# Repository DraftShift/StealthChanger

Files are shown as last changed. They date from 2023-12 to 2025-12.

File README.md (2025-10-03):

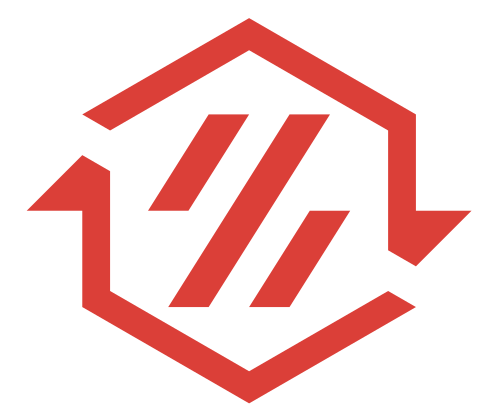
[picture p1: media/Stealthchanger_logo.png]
#  StealthChanger
**Tool changing system for Vorons and other front mount printer motion systems.**


&nbsp;&nbsp;&nbsp;&nbsp;&nbsp;&nbsp;


## Introduction

Unlike the name suggests we support more then just stealthburner.

Due to difficulties with heat insert and aligning of bearings and mounts we wanted to try a more simplistic design based on bushings and pins.

This is a very light design, requiring less parts and as such is cheaper and easier to build.  Input shaper tests have shown it to be as rigid if not more than current Tapchanger.

All parts are easily replaceable without reprinting if wear happens, life of the bushings and pins are still being tested.

## Tool compatability
Currently we support the standard Stealth Burner, Dragon Burner, Rapid Burner, Yavoth, AntHead, A4T, XOL, Jabberwocky and Archetype BlackBird.  There is also a usermod for the [Mini Stealth Burner](UserMods/jdmontgomer/MiniSB_SC).

## V1.1 Release
The original StealthChanger shuttle and backplates have been updated to V1.1, this update is to improve rigidity and probe accuracy. To help identify the version, "V1.1" has been clearly marked on all shuttles and backplates. please note, V1.1 is NOT compatible with previous versions. Updated documentation will follow shorly.
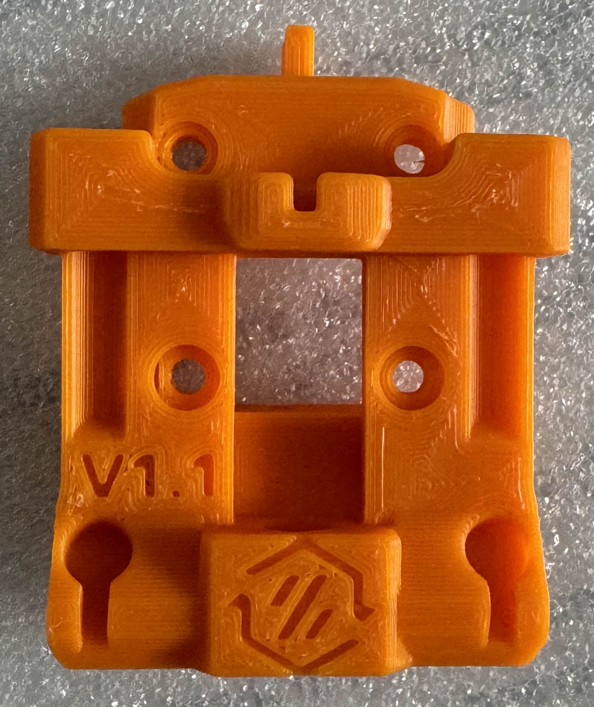
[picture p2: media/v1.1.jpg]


## Documentation and Info

Please use our [wiki](../../wiki) for more information and documentation.

- [Bill of Materials](../../wiki/Bill-of-Materials)
- [Docks](../../wiki/Docks)
- [Printing](../../wiki/Printing)
- [Assembling](../../wiki/Assembling)
- [Installation](../../wiki/Installation)
- [Configuration](../../wiki/Configuration)
- [Calibration](../../wiki/Calibration)
- [Slicers](../../wiki/Slicers)
- [Serials](../../wiki/Serials)
- [Support and FAQs](../../wiki/Support-and-FAQs)
- [Contributing & Donating](../../wiki/Contributing-and-Donating)
- [Team & Credits](../../wiki/Team-and-Credits)
- [Vendors & Kits](../../wiki/Vendors-and-Kits)

## Preview
### Explaination Video featuring GMBridge
MRRF Interview (https://www.youtube.com/watch?v=iQx_yx1GapI)
### Printed Parts (Dragonburner) by BT123
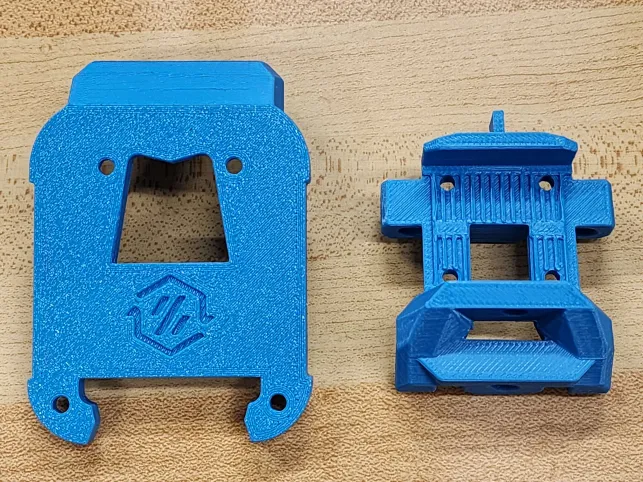
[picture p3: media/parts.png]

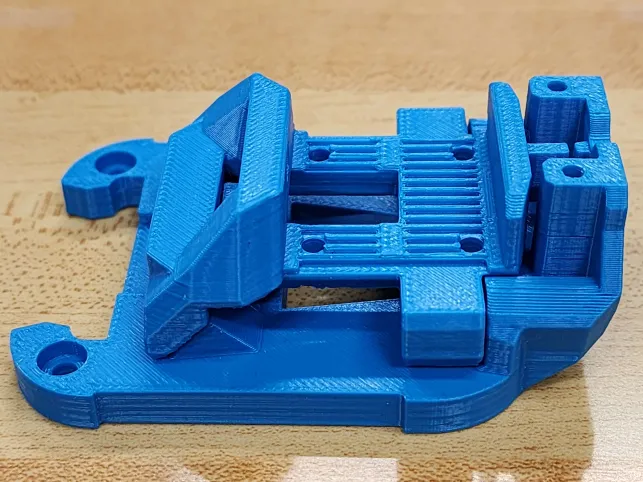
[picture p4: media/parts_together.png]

### Important! - Check for clear Hex's (Dragonburner) by BT123
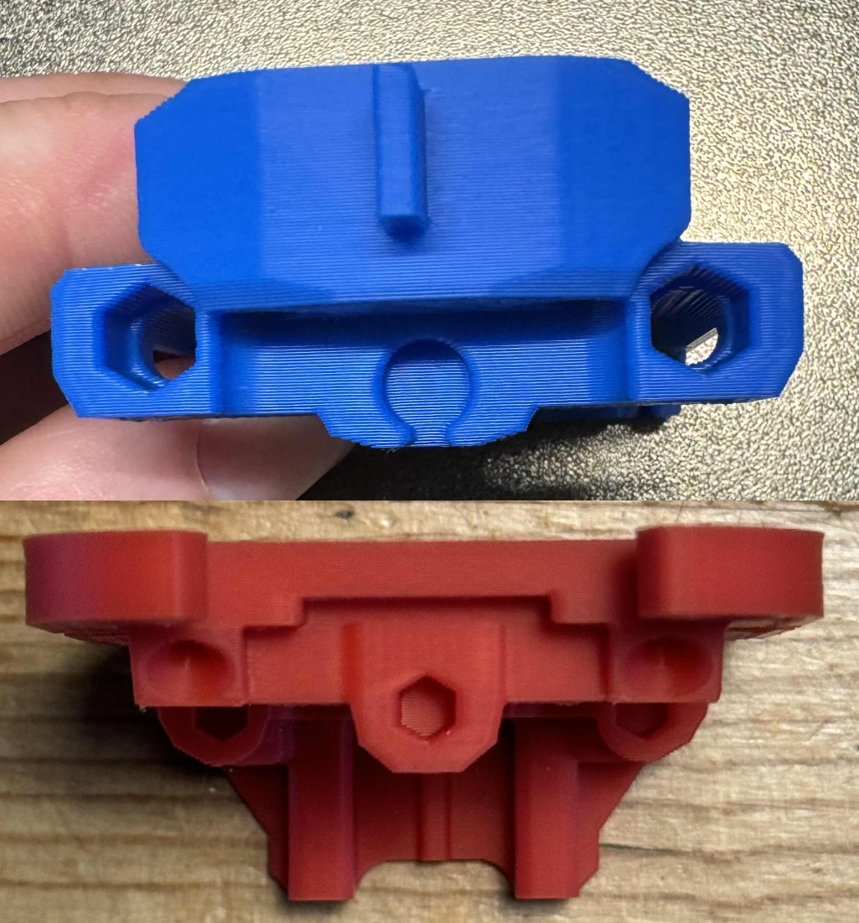
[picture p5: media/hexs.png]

### Assembled Shuttle and Backplate by BT123

### Motion (Stealthburner) by TheSin-

### Docking (Stealthburner) by fiferboy


Originally based on Viesturz's [Tapchanger](https://github.com/viesturz/tapchanger)

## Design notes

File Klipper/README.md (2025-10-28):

# Example Setup

Most of the code has been taken from the [TapChanger](https://github.com/viesturz/tapchanger) repo.

## Tapchanger Files

You need
- `homing.cfg`, `macros.cfg`, and `toolchanger.cfg` from [TapChanger Examples/per tool probe](https://github.com/viesturz/klipper-toolchanger/tree/main/examples/z%20probe/per%20tool%20probe)
- [`tool_detection.cfg`](https://github.com/viesturz/klipper-toolchanger/blob/main/examples/tool_detection.cfg)

You can either add them manually to your klipper install, or alternatively, you can integrate them to your config so that moonraker keeps them up to date with your other software if they change. Below are the steps for the integrated way. If you make any changes to the files though, they will be overwritten if you update. If you choose to manually add them, make sure your printer.cfg reflects the location of them.

**On the Klipper System** 
```
cd ~
git clone https://github.com/viesturz/tapchanger.git
ln -s ~/tapchanger/Klipper/config-example ~/printer_data/config/tapchanger
```

**Add to moonraker.conf**
```
[update_manager tapchanger]
type: git_repo
path: ~/tapchanger
origin: https://github.com/viesturz/tapchanger.git
primary_branch: main
managed_services: klipper
```

## Klipper Toolchanger

You must install [klipper-toolchanger](https://github.com/viesturz/klipper-toolchanger/), Follow instruction on the linked page.

## Toolheads

Toolchangers start with number 0, and count up. So for all the configs, make sure you change all sections. IE, in your T1 config, make sure its extruder1, fan1, etc. See the examples.  **NOTE: The only except to this rule is T0 extruder has no number.**

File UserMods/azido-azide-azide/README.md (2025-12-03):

# Monolith gantry with fixed beltpath issues which arises by using the monolith beltpath with the (cnc) stealthchanger shuttle
The belts are aligned by offsetting the X-axis from its previous location ~2.26mm to the back. When the CNC shuttle is used just clamp the belts only in the front.



## The file V2 mod. Monolith Stealthchanger compl. is a derivative work from CloakedWaynes monolith gantry. This gantry is modified to use mgn12 on all three axis  



## The file Sheetmetal 9mm AWD X-axis Stealthchanger compl. modifies just the monolith XY joints to fix the belt issues



## The file Printed 6mm 2WD X-axis Stealthchanger compl. modifies just the monolith XY joints to fix the belt issues



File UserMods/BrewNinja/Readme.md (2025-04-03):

Anthead Mods

 - There is an improved printing version of N3MI's Voron Sherpa spaced Stealthchanger main body. No supports needed.
 - Second version of N3MI's main body with more space above the diffuser/PCB. Read that folder for more info.
 - Thin SC diffuser for resin printing.
 - HGX adapter plate. This fits any of the anthead sherpa spacing bodies. You really don't need this except if you want to run the wires up the back.

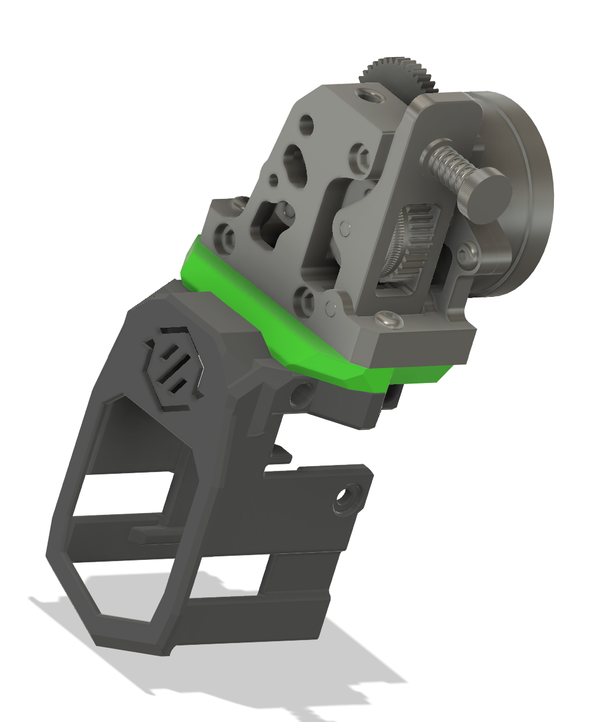
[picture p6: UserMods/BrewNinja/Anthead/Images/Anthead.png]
Anthead Mods Pic


If you have questions about any of my mods, you can find me on the Stealthchanger Discord.

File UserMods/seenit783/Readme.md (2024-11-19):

# EBB36 and Galileo 2 Standalone User Mod

## Overview

This user mod provides compatibility between the [EBB36](https://example.com/ebb36) and the [Galileo 2 Standalone](https://github.com/JaredC01/Galileo2/tree/main/galileo2_standalone) system. The mod enables seamless integration, allowing users to utilize these two components together efficiently.

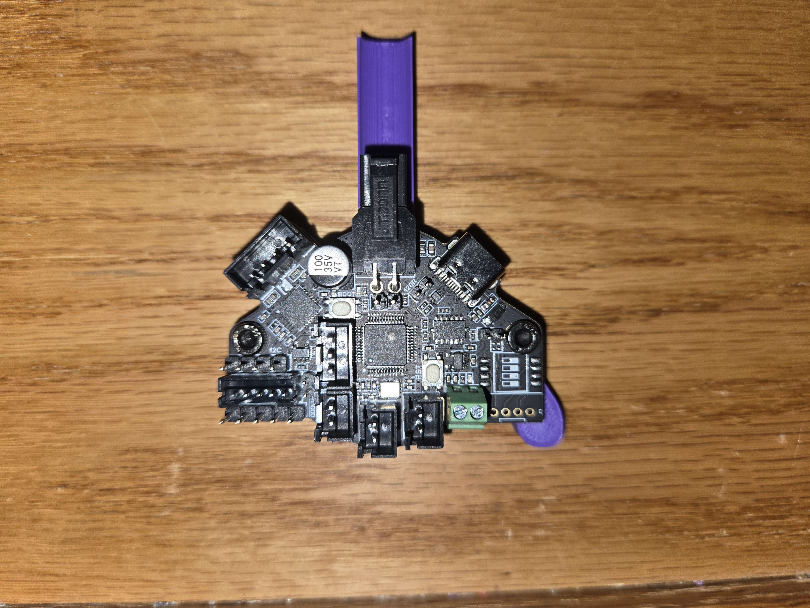
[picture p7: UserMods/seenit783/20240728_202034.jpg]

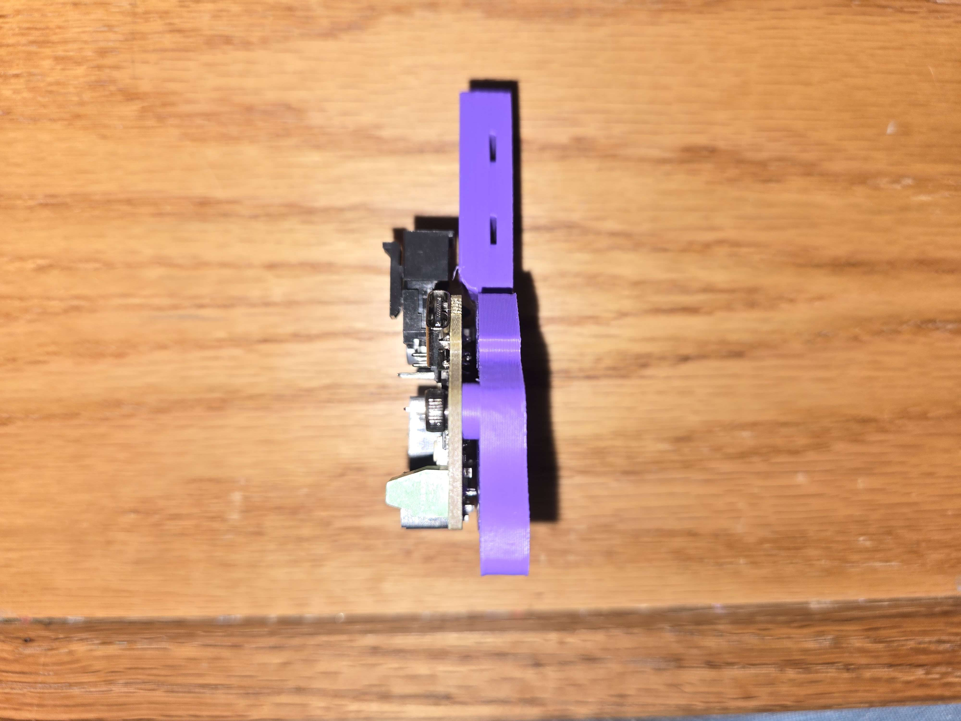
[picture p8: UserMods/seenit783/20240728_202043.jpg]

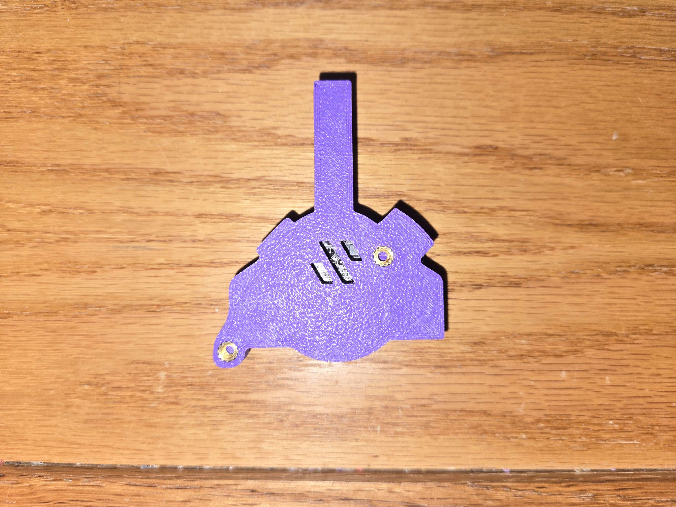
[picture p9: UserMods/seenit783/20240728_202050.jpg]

*Image of the Galileo 2 Stand Alone device*

Galileo 2 Standalone  
*Image of the Galileo 2 Standalone system*

## Features

- **Compatibility**: Ensures that the EBB36 can directly interface with the Galileo 2 Standalone.

## Installation
2 - M3x40 cap bolts with 100% Threads https://a.co/d/dL6dTwI 
4 - M3x5x4 Threaded inserts https://a.co/d/jbFK0In

1. **Download the Mod**: Obtain the latest version of the user mod from the [releases page](UserMods/seenit783).

2. Refer to the [Galileo 2 Standalone configuration guide](https://github.com/JaredC01/Galileo2/tree/main/galileo2_standalone) for detailed configuration instructions.

## Contributing

If you have suggestions for improvements or encounter bugs, please open an issue on the [GitHub repository](https://example.com/issues). Contributions are welcome, and you can submit a pull request to enhance the mod.

## License

This mod is licensed under the [MIT License](https://example.com/license). See the `LICENSE` file for more details.

## Contact
Angus MacLeod On Discord

For further assistance, you can contact the mod author at [richardferrington@gmail.com](mailto:richardferrington@gmail.com).
Angus MacLeod on Discord
---

Thank you for using the EBB36/Galileo 2 Standalone User Mod. We hope it enhances your experience with your toolheads!

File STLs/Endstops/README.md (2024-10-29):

# Endstops

There are a few options availble for x/y endstops. All options remove the X chain as it's not used with SC at all.

1. Hall Effect: Using the normal Voron X/Y Join hall effect board, download and print the [Hall_Effect.stl](Hall_Effect.stl) or [Hall_Effect_Shuttlekepper.stl](Hall_Effect_Shuttlekepper.stl) if you are use shuttle keeper.

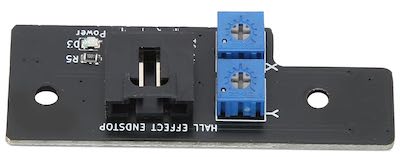
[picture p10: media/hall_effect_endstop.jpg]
Hall Effect board


2. Switches: Using the normal Voron X/Y Join switch board (both switches are on the x/y join together like hall effect.  Download and print the [Hall_Effect.stl](Hall_Effect.stl) or [Hall_Effect_Shuttlekepper.stl](Hall_Effect_Shuttlekepper.stl) if you are use shuttle keeper, this will add the needed surface for the X switch to hit.

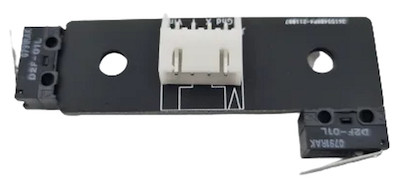
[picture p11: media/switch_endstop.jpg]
Switches board


3. Relocated Switches: This will relocate both X/Y to the rear A Motor brackets.  This has the added benefit of removing the Y chain completely.  Download and print [[a]_switch_bracket.stl]([a]_switch_bracket.stl) and [[a]_switch_arm.stl]([a]_switch_arm.stl).

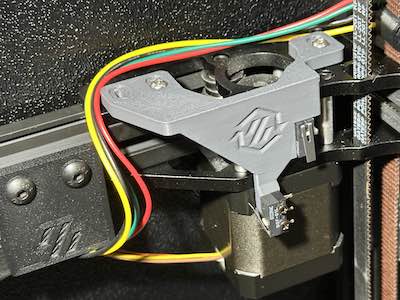
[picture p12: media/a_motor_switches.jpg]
Relocated Switches


4. Sensorless: Of course you always have the option of sensorless homing for X/Y which also allows you to completely remove the Y chain.  But you have less wires and nothing to print in this case.

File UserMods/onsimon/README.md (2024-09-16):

# Orbiter V2 BTT EBB36 carrier

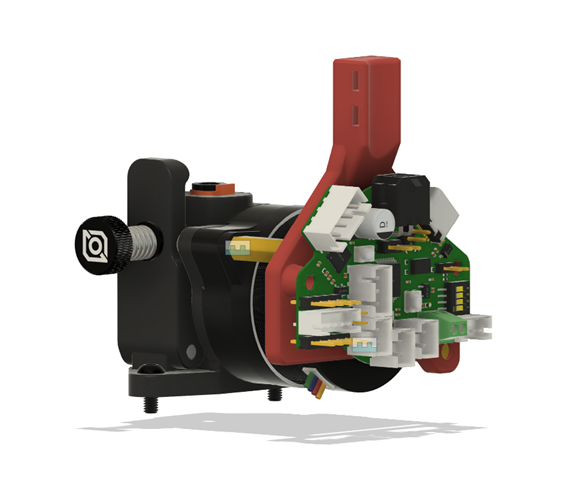
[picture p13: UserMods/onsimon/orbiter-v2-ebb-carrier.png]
orbiter-v2-ebb-carrier
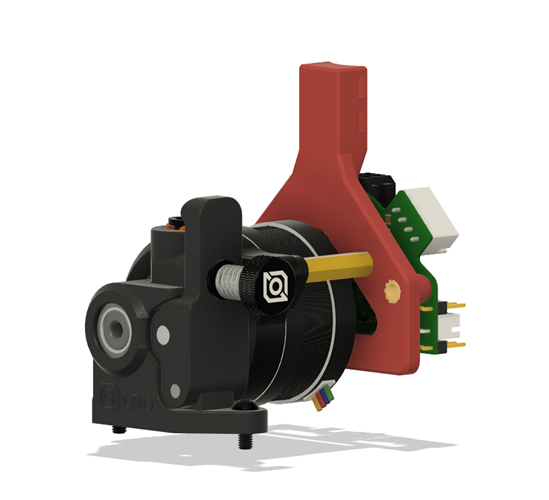
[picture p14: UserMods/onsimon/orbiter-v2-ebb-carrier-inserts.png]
orbiter-v2-ebb-carrier
 

Since the extuder motor on Orbiter V2 sits quite low, the EBB36 will interfere with the optotap PCB on some toolhead backplates (Dragon Burner and Yavoth, maybe more). So I created this PCB carrier that places the EBB36 a few mm higher than other existing mounts, and also tried to make it as rigid as possible without extra structures or modifications. 

Parts:
* Standoffs included with the EBB36
* 2 M3 BHCS to secure the mount agianst the standoffs
* 2 M3 SHCS to secure the EBB36 to the mount
* Optional: 2 M3 5x4 heat inserts (print the corresponding STL)

It is modelled to real-world dimesions and works fine as-is with ABS for me, but you can consider slicing with appropriate shrinkage compensation for your specific filament for the best possible fit.

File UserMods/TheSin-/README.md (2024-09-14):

# Mods to Stealthchanger v1.x

- **Hall Effect Bracket** with a 5mm shift to deal with shuttle keeper moving the shuttle out 5mm. Hall Effect setup comes from the Voron Team in the original 2.4R2 CAD

- **Z stop** is an original design and allows for the shuttle to use a standard Voron Z End Stop to home the shuttle without a tool or to avoid using tap to home.

- **SV08 Dockbar Brackets**

- **PCB36 Mount** is an Fly SHT36/Nitehawk 36 PCB mount for SC with HGX CNC/Orbitor2 Extruder.  Requiers a 20mm standoff.  Original PCB mount is from [MapleLeafMakers](https://github.com/MapleLeafMakers), updated to fit V3.

- **Belt Covers** For Voron v2, orignal from [Akio in the Voron Usermods](https://mods.vorondesign.com/details/LzEFU0RDHXUarF7y69x2Q), build with the SC Logo in open or raised for 2 colour printing

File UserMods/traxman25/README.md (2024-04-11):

## 5.5mm OD Bushing mod
Mod to the stock Stealth Changer shuttle to use 5.5mm OD bushings from Mc MasterCarr. More info and a link to the bushings is included in that directory. 

## Custom Dragonburner upgrades
These parts mod the Dragonburner tool head with optional numbered cowl and EBB36 mount. The EBB36 mount is designed to work with the Orbiter v2.0 extruder on the tall mount.

Original cowl by chirpy2605 [here](https://github.com/chirpy2605/voron)

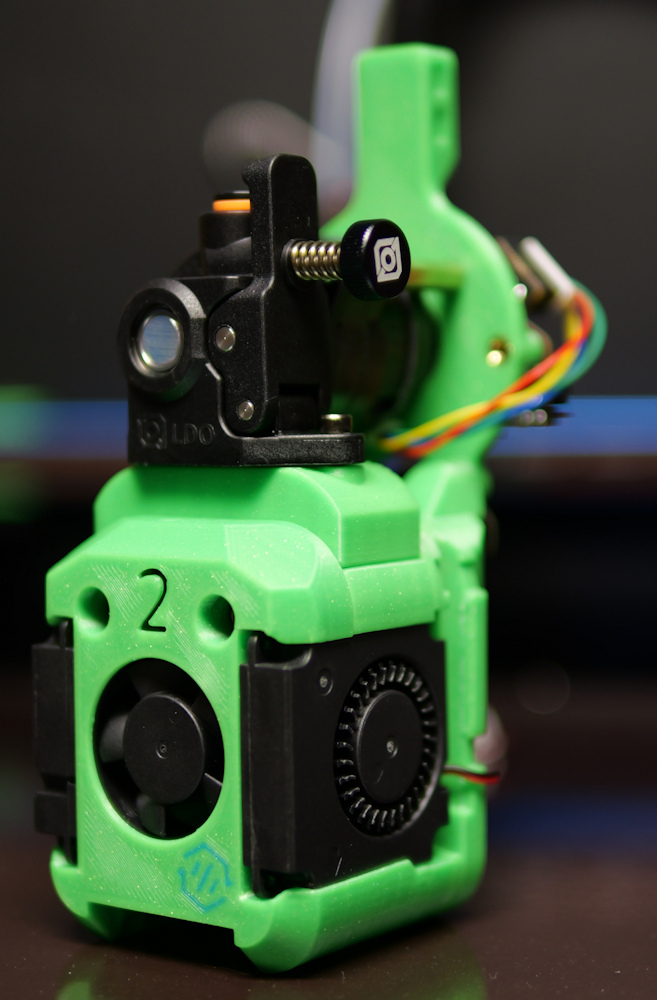
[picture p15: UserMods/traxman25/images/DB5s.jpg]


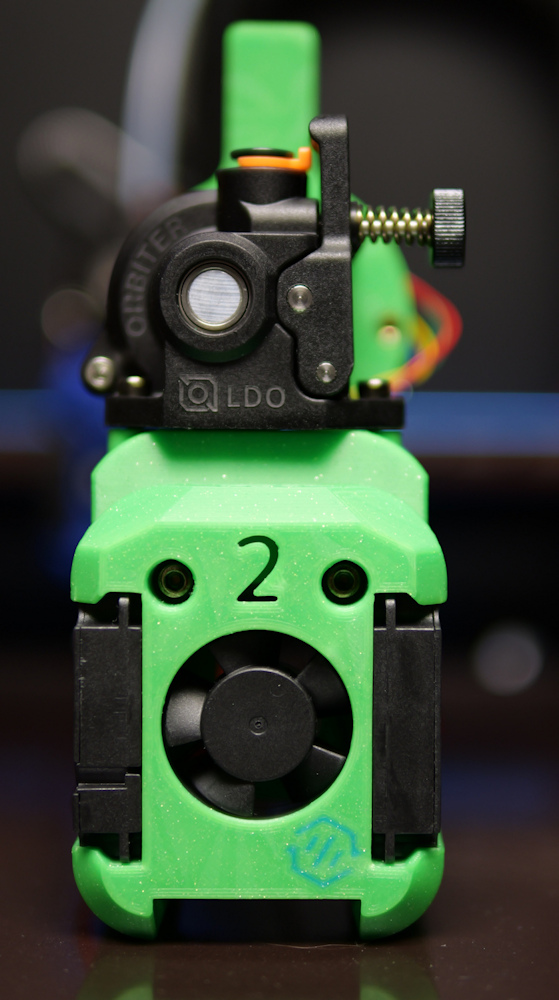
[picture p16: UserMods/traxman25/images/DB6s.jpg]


## Custom Dragonburner Cowls
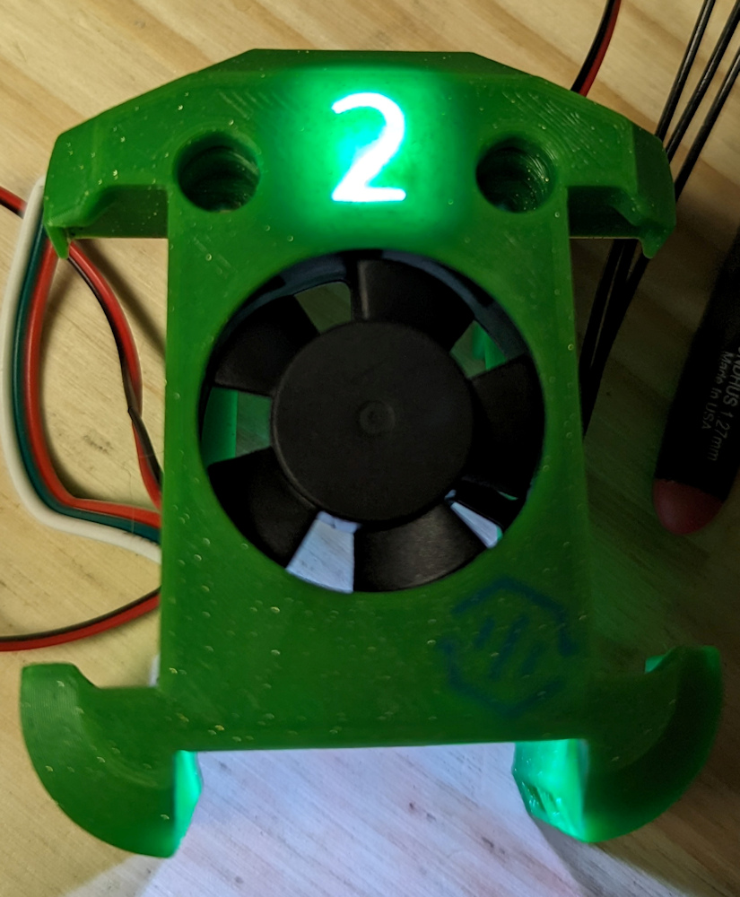
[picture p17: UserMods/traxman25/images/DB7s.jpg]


A series of Tap Changer Hook On Dock style Cowls based on Viesturz modification of Chirpy2605’s Dragonburner Cowl [here](https://github.com/viesturz/tapchanger/blob/main/Tapchanger/STL/Toolheads/DragonBurner/Cowling.stl).  These are modified to have the upper tool head light display the tool number. The Stealth Changer logo is applied as a second object (color) in the lower right corner. The STEP file for each tool head has the SC Logo embedded. To make them multi colored simply open each numbered cowl in your slicer as one object and then change the color for each part.

Also included are the numbered diffusers for each number. Numbers available are 0-6 so you can do up to 7 tools or pick and choose if you want them to start with 0 or 1.

You’ll also need the LED carrier for whichever LED you’ll be using. The RGBW Carrier is for the round 3 wire LEDs that are similar to what is included in the LDO kits. A carrier for Sequin LEDs is also provided for the small RGB Sequin LEDs that have 4 solder pads on them. Generally speaking, the round RGBW LEDs are much easier to wire.

A build plate with all tool heads and parts already oriented is provided. You’ll need to clone whichever version of the LED mount that you need and delete the one you don’t need. DB Numbered tool heads.3mf

## Dragonburner_EBB36_SC_Mount
All 3 parts described below are included in the DragonBurner_EBB36_OrbiterV2_mounts.STEP step file, and also on a pre-oriented and pre-support painted build plate in the .3mf file. 

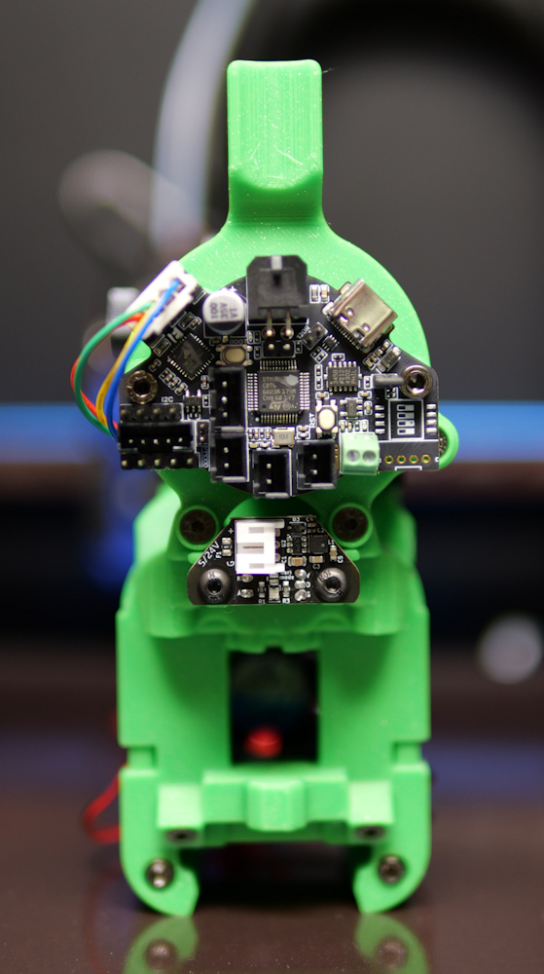
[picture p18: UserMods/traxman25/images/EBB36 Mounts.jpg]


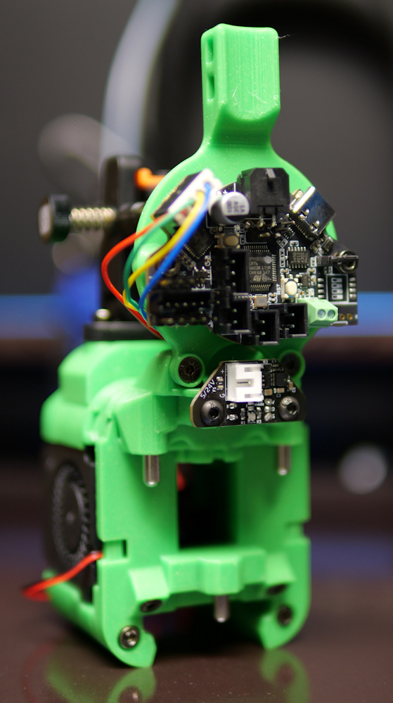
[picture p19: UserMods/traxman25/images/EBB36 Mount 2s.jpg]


### Dragon Burner EBB36 Backing Plate 
The only change to this part is adding the tool head PCB mount support ears to the top. These 2 holes will get an M3 heat set insert. This is modified from Stealthchanger’s back plate.

### EBB36 mount
Mounting plate with lower support screw holes that is similar to Chirpy2605’s mount. However, Chirpy2605’s original mount interferes with the DB Backing Plage. This mod also centers the EBB36 to the tool head assembly better.

Chirpy2605’s original version from [here](https://github.com/chirpy2605/voron/tree/main/general/PCB_Mounts/STLs)

### Orbiter V2.0 Extended Dragonburner Mount 
Minor cosmetic change to Chirpy2605’s Extended Dragonburner Orbiter V2.0 Mount. Unused holes that show above the cowl are removed.

The original mount is available [here](https://github.com/chirpy2605/voron/blob/main/general/Alternative_Voron_Mounts/Extended_Extruder_Mounts/Orbiter2_Extruder_Mount.stl)

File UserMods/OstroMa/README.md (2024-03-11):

# Mods for Stealthchanger

Dragonburner cowl mods based on work from the orignal cowl by [chirpy2605](https://github.com/chirpy2605/voron)

## Cowl moded to use the tapchanger hookon dock

## Numeric diffusers which are clip in to the Voron logo on Dragonburner and should work with Stealthburner

## 6 colour calibration print to help set x/y offsets between tools

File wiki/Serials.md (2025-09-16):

1. [Requests](#requests)
2. [List](#list)

## Requests

**Serial Application Guide Lines**

**Make sure media is 25MB or less (youtube link allowed, no limit)**

**Only one post per serial request**

**Post a video here that shows (we shouldn't need to pause, zoom, jog a video, it's your responsibility to make sure it's clear and easy to see at normal play speed)**

* 2 tool min print (mid print is fine)
* clearly shows a tool change
* clearly shows the StealthChanger shuttle
* a picture of the finished print is a bonus!
* some form of visual with your discord username and date (within the last 24 hours) on it in the video

**NOTE: tool calibration prints do not count**

Submit the request to the `#serial-request` channel on our [Discord](https://discord.gg/jJs73c6vSc).

## List

The list is available on our [Discord](https://discord.gg/jJs73c6vSc) in the `#serials` channel.

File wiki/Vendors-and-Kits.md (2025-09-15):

Currently we are working with Manufacturers and Vendors on official kits and CNC parts.  Once available and officially tested they will be listed here in alphabetical order.

# World Wide Vendors World Wide

## [LDO Motion](https://ldomotion.com/)

Each kit bellow includes a `Where to buy` on the product page.

- [Base Kit](https://ldomotion.com/products/16607023627247272)
  - CNC Shuttle
  - Sex Ball probe
  - NH-Hexa 6+1 port USB adapter
- [Tool & Dock Kit](https://ldomotion.com/products/16607023627247272)
  - Nitehawk-36 Toolhead Kit (SC-edition)
  - OptoTap PCB
  - RGB Sequin/NeoPixel
  - High CFM LDO fans (1x2510 axial, 2x4010 blower)
  - Backplate Pins
- [Top Hat & Door Buffer Kit](https://ldomotion.com/products/16607023627247272)
  - LDO quality extrusions
  - Fasteners and hardware
  - Panels

# Canadian Vendors Canada Flag

## [bobcat3d](https://bobcat3d.etsy.com/)
On Discord: Broncosis

- [Essential Hardward](https://www.etsy.com/ca/listing/1736497017/voron-stealth-changer-essential-hardware)
- [Opto Tap Sensors](https://www.etsy.com/ca/listing/1769077964/voron-opto-tap-sensors)

# USA Vendors US Flag

## [Fabreeko](https://www.fabreeko.com/)

- [Fysetc CNC Shuttle](https://www.fabreeko.com/products/stealth-changer-cnc-shuttle-kit-by-fysetc)
- [Fysetc Can Bus Distribution Board](https://www.fabreeko.com/products/can-bus-distribution-board-for-stealth-changer-by-fysetc)

## [Isik's Tech](https://store.isiks.tech/)
On Discord: xbst_

- [Birds' Nest](https://store.isiks.tech/products/birds-nest)
- [MOAR_CAN](https://store.isiks.tech/products/moar_can)
- [XT30+2 CAN Cable](https://store.isiks.tech/products/xt302-2-can-cable-3-meters)

# International Vendors

## [Fystec](https://www.aliexpress.com/store/3480083)

- [CNC Shuttle](https://s.click.aliexpress.com/e/_ooNmh4z)
- [Can Bus Distribution Board](https://s.click.aliexpress.com/e/_ooNmh4z)

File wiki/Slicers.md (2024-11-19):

1. [Slicer Software](#slicer-software)
2. [Slicer GCODEs](#slicer-gcodes)

## Slicer Software

| Name | Multitool | Issue | Discussion | Notes |
|:---:|:---:|:---:|:---:|---|
| Cura | <span style="color: green;">✓</span> | | | As of 5.8, select new printer, select DraftShift Design, select the size from the voron list, allows up to 8 extruders |
| OrcaSlicer | <span style="color: green;">✓</span> | | | As of 2.2 |
| PrusaSlicer | <span style="color: green;">✓</span> | | | |
| Simplify3D | <span style="color: silver;">?</span> | | | |
| Slic3r | <span style="color: silver;">?</span> | | | |
| SuperSlicer | <span style="color: green;">✓</span> | | | See [2197](https://github.com/supermerill/SuperSlicer/issues/2197) |

## Slicer GCODEs

### Prusa

Printer -> Custom G-code -> **Start G-code** - all must be a single line
```
PRINT_START TOOL_TEMP={first_layer_temperature[initial_tool]} {if is_extruder_used[0]}T0_TEMP={first_layer_temperature[0]}{endif} {if is_extruder_used[1]}T1_TEMP={first_layer_temperature[1]}{endif} {if is_extruder_used[2]}T2_TEMP={first_layer_temperature[2]}{endif} {if is_extruder_used[3]}T3_TEMP={first_layer_temperature[3]}{endif} {if is_extruder_used[4]}T4_TEMP={first_layer_temperature[4]}{endif} {if is_extruder_used[5]}T5_TEMP={first_layer_temperature[5]}{endif}  BED_TEMP=[first_layer_bed_temperature] TOOL=[initial_tool]
```

Printer -> Custom G-code -> **Tool change G-code**
```
M104 S{temperature[next_extruder]} T[next_extruder] ; set new tool temperature so it can start heating while changing
```

**NOTE**: add this as a second line if you use prime tower
```
G1 X{wipe_tower_x} Y{wipe_tower_y} F{travel_speed*60} ; Move to wipe tower before tool change
```

### Orca

Printer settings -> Machine G-code -> **Machine start G-code** - all must be a single line
```
PRINT_START TOOL_TEMP={first_layer_temperature[initial_tool]} {if is_extruder_used[0]}T0_TEMP={first_layer_temperature[0]}{endif} {if is_extruder_used[1]}T1_TEMP={first_layer_temperature[1]}{endif} {if is_extruder_used[2]}T2_TEMP={first_layer_temperature[2]}{endif} {if is_extruder_used[3]}T3_TEMP={first_layer_temperature[3]}{endif} {if is_extruder_used[4]}T4_TEMP={first_layer_temperature[4]}{endif} {if is_extruder_used[5]}T5_TEMP={first_layer_temperature[5]}{endif}  BED_TEMP=[first_layer_bed_temperature] TOOL=[initial_tool]
```

Printer settings -> Machine G-code -> **Change Filament G-code**
```
;Leave blank
```

### Cura

Machine Settings -> Printer -> **Start G-code** - all must be a single line
```
PRINT_START TOOL_TEMP={material_print_temperature_layer_0} T{initial_extruder_nr}_TEMP={material_print_temperature_layer_0} BED_TEMP={material_bed_temperature_layer_0} TOOL={initial_extruder_nr}
```

Machine Settings -> Printer ->  Tool n -> **Extruder Start G-code**
```
;Leave blank
```

Machine Settings -> Printer ->  Tool n -> **Pre tool change G-code** - 5.10+
```
M104 S{material_print_temperature} T{extruder_nr}
```

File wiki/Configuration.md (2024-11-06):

Toolchangers start with number 0, and count up. So for all the configs, make sure you change all sections. IE, in your T1 config, make sure its extruder1, fan1, etc. See the examples.  **NOTE: The only except to this rule is T0 extruder has no number.**

1. [Toolhead Configuration](#toolheads-configuration)
2. [CANbus](#canbus)
3. [Offsets](#offsets)
4. [Dock Positions](#dock-positions)
5. [close_y and safe_y](#close_y-and-safe_y)
6. [Docking Path](#Docking-Path)

## Toolheads Configuration

Please see the repo files for more info on these. [Configuration Files Repo](https://github.com/DraftShift/StealthChanger/blob/main/Klipper)

You need to add the info in `printer.cfg` from our repo to your `printer.cfg`

You need to have a separate toolhead config for each toolhead, then link those in your `printer.cfg`, as well as removing/moving the current extruder/hotend config from your `printer.cfg` file. See the examples in the repo for more information and a starting place. You will have to edit them with your own values.

**NOTE:** for some odd reason `t_command_restore_axis` was set to blank recently, this should be `t_command_restore_axis: z` please make sure that is your setting.

**NOTE:** `_PARK_ON_COOLING_PAD` is a useless macro in `PRINT_START` in `macros.cfg` please make sure to comment out or remove that line, currently it is line 129.

## CANbus

[Esoterical CANbus](https://github.com/Esoterical/voron_canbus) this is a pretty definitive guide for canbus implementation on klipper.

**Example CANbus layout**

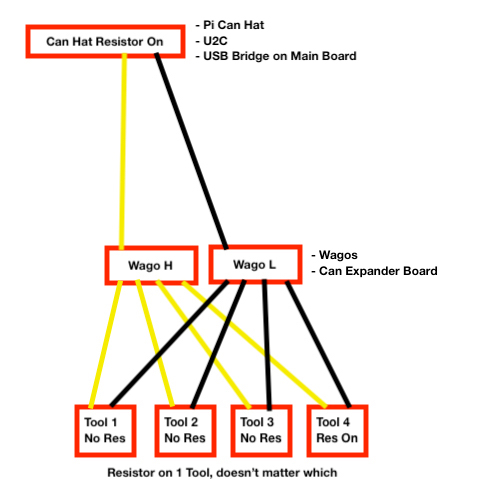
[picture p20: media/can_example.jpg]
Example CANbus Layout


## Offsets

There are 2 places to set offsets in your toolhead config files. There is gcode_(x/y/z)_offset in the [tool] section, and (x/y/z)_offset in the [tool_probe] section. These do different things. The ones in the [tool] section are always relative to a specific tool. IE, if you homed with T0, then the gcode offsets are relative to T0. When you do multi-material prints, you will have to choose 1 tool to always do the homing, even if you don't use it, because all the other offsets need to be set against it. The [tool_probe] offset is only ever applied when homing with that tool. The gcode offsets are applied when changing a tool.

You should set all the `[tool_probe]` offsets as well though. If you are only using a single tool, you can home with that tool, and it will use the offset in the `[tool_probe]` section. You won't need to home with your primary tool first then before you start a print. 

To try and further clarify. Lets say you have 3 tools, T0, T1, and T2. We will say that T0 is your "primary" tool. Setup the probe z_offset like you would any other printer. Make sure the offset is set in `z_offset` (IE, make sure when you home and go to Z 0, the nozzle is actually in that spot). Its location in x/y/z is always going to be 0 in relation to the other tools. So after T0 is homed, T1 and T2 (may) need to have their `gcode_(x/y/z)_offset` changed so they match the location that the primary tool actually is. There are 2 main ways of doing this. You can use a test print to print layers on top of or next to each other (something like this: [Nozzle Alignment Assist](https://www.printables.com/model/109267-nozzle-alignment-assist)) or you can use a camera (something like [kTAMV Klipper Tool Alignment](https://github.com/TypQxQ/kTAMV) or [IDEX Nozzle Calibration Tool](https://github.com/Life0fBrian/Brians-IDEX-Nozzle-Calibration-tool)).

## Dock Positions

When setting your dock position in your tool config, X and Y are pretty self explanatory. Put the tool in the right spot for it to sit. However, Z should be the point where 1 more mm down will untrigger the tap module. 

## close_y and safe_y

It is important to get this right. If you don't, you will have changing issues, or crash your tools into your docks. This is where we recommend you start:

- close_y = park_y + 30
- safe_y = park_y + thickness of your thickest tool (plus a little buffer)

IE, if you Y park position is -15. Your close Y should be 15. If your Y park position is 0, it should be 30. Safe Y should be slighty further out. 

## Docking Path

The docking path can be confusing for people to understand. Let's try to disect it. Take this path:

params_sc_path: [{'y':9.5 ,'z':4}, {'y':9.5, 'z':2}, {'y':5.5, 'z':0}, {'z':0, 'y':0, 'f':0.5}, {'z':-10, 'y':0}, {'z':-10, 'y':16}]

When looking at this, understand that the movements are relative to the park position. When dropping off a tool, it will go left to right, and when picking up a tool, it will go right to left on movements. Let's say your park position is x=20 y=-10, z=240 and close_y=20. When dropping off a tool, it will move up and start the sequence essentially at x=20 y=20 z=240. Now add in the first set of items. 

*  {'y':9.5 ,'z':4} Move to x=20 y=-0.5 z=244
*  {'y':9.5, 'z':2} Move to x=20 y=-0.5 z=242
*  {'y':5.5, 'z':0} Move to x=20 y=-4.5 z=240
*  {'z':0, 'y':0, 'f':0.5}. This will slowly move you (f is speed in gcode) to docking position of x=20 y=-10, z=240
*  {'z':-10, 'y':0} Drop the z down to z=230 so that it starts unhooking.
*  {'z':-10, 'y':16}. Move to z=230 y=6, we are clear of the tool.

It will then move to the close_y and x of the tool its picking up, and run in reverse order.

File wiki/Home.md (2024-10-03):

#  StealthChanger

Stealth Changer is a friction and magnetic fit, 3d printing multiple tool changer for the Voron 2.4 printer.

The purpose of a multiple toolhead changer is to allow for mixed material and mixed color printing without having to manually swap filament or purge filament during the swapping of materials. This allows for faster printing and less wasted filament compared to manual swapping and multi-material units like the ERCF or an AMS system.

It consists of a toolhead shuttle, toolhead backplate, and a optotap sensor for Z probing.

Stealth Changer supports a number of popular toolheads by mounting a backplate to the toolhead while using existing toolhead mounting points.

The shuttle replaces the current Voron TAP or Voron X carriage frame while using the TAP optotap sensor.

Mounting of the toolhead with the shuttle is done by using bushings and pins, with magnets to help create a strong mounting connection for high-speed printing while also providing better inputshaping results than TAP.

This is a very light design, requiring less parts and as such is cheaper and easier to build.  Input shaper tests have shown it to be as rigid if not more than current Tapchanger.

All parts are easily replaceable without reprinting if wear happens, life of the bushings and pins are still being tested.

The number of docks that can be installed is based on the width of the printer and the X/Y joins that allow the shuttle to reach the left and right side docks.

## Tool compatability
Currently we support the standard Stealth Burner, Dragon Burner, Rapid Burner, Yavoth, XOL and Archetype. There is also a usermod for the [Mini Stealth Burner](../blob/main/UserMods/jdmontgomer/MiniSB_SC).

## Before you begin

Make sure to visit our [Checklist](Checklist)

There are a few considerations that should be taken into account before you begin this project. First is, yes, you need an optotop board on every tool. The board is needed as thats how klipper knows which board is active. When the tap sensor is triggered, it knows which tool it has. You do not need the other tap parts though, like the MGN9 rail. StealthChanger by design also acts like the normal tap and does z probing.

Are you going to be printing any material that needs an enclosed printer? If the answer is yes, then you will need a tophat on your printer (or longer vertical extrusions). Typically, it adds around 200mm to the top (give or take based on your specific build). 

Canbus is nearly a requirement. While technically you dont need to do canbus, getting that many wires to each tool and doing so in a way that they won't tangle is going to be a nightmare. That being said, cable management is a very big part of the process. Without it, the cables will get wrapped up around each other and cause issues. Having some kind of plan for umbilicals is a must when considering the project.

How are you doing docks? There are a few different ways of doing them, and what you choose is going to influence a lot of things. If you plan on using a stock Voron build, remember that you need to have clearance at the sides of the docks for the front idlers to go beside them. This will also influence number of tools. You also have the option of top rail mounted docks or crossbar docks. Crossbar docks are probably the most stable, as they ultimately can be more stiff. You can also do a crossbar plus topmount for even more rigidity. If you decide to go this route, then you really want to use 2040 extrusions for your front rails. This way you can still use all the stock voron doors/panels etc with the crossbar, as well as not have the idlers hitting the crossbar. Top mounted docks are completely acceptable though, they just have a little more movement to them. As an alternative option the team has created a printable [door buffer](https://github.com/DraftShift/DoorBuffer) that will give you a crossbar without requiremend to replace your current front frame.

1. [Bill of Materials](Bill-of-Materials)
2. [Docks](Docks)
3. [Printing](Printing)
4. [Assembling](Assembling)
5. [Installation](Installation)
6. [Configuration](Configuration)
7. [Calibration](Calibration)
8. [Slicers](Slicers)
9. [Serials](Serials)
10. [Support & FAQs](Support-and-FAQs)
11. [Contributing & Donating](Contributing-and-Donating)
12. [Team & Credits](Team-and-Credits)
13. [Vendors & Kits](Vendors-and-Kits)

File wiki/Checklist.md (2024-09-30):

 - [ ] Read and understand all the documentation
 - [ ]  Decide on the tools to use, See [Docks](Docks) for a calculation of how many will fit
 - [ ] Decide on dock types, [Modular Dock](https://github.com/DraftShift/ModularDock) or other
 - [ ] Decide if you are going top mount, or use a cross bar, 2040 or [Door Buffer](https://github.com/DraftShift/DoorBuffer) or [MiniBFI](https://github.com/DraftShift/StealthChanger/tree/main/UserMods/BT123/MiniBFI%20%2B%20MicroBFI)
 - [ ] Decide on a [Tophat](https://github.com/DraftShift/Tophat)
 - [ ] Decide on umbilical management **WIP**
 - [ ] Visit the [BOM](Bill-of-Materials) to make sure you have ordered everything you need for the convertion
 - [ ] Visit our [Printing](Printing) guide and start printing
 - [ ] At this point please inspect your prints, take extra note that your hexes are very uniform, if the tops are flat you will have alignment issues, it doesn't take much for things to start off wrong here.
 - [ ] [Assemble](Assembling) the shuttle and backplates
 - [ ] [Install](Installation) software
 - [ ] [Configure](Configuration) software
 - [ ] Calibrate [Z Offsets](Calibration#z-offset)
 - [ ] Calibrate [Dock Parking](Calibration#dock-parking)
 - [ ] Calibrate [X/Y Offsets](Calibration#xy-offset)
 - [ ] Registrer for a [serial](Serials)
 - [ ] Visit our [sponsor](https://github.com/sponsors/DraftShift) page

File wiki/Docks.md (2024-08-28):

The team has created their own dock as a solution. It allows for mounting from both the top bar, as well as a crossbar (or both). While its currently still in testing, its an option if you can do some work without having a full readme. You can view it here: [DraftShift Modular Dock](https://github.com/DraftShift/ModularDock)

Currently all docks used with [Viesturz's Tapchanger](https://github.com/viesturz/tapchanger) are compatible.

To calculate how many tools you can fit on the front of your printer you ened to know the tools to use first and the amount of room for your front idlers (stock gantry also can't move the entire length of X so make sure you factor that in as well.

   - Dragon Burners/Yavoth require 60mm per tool (I recommend 5mm between for extruder handles)
   - Blackbird, Stealth Burners and XOL require 76mm per tool
   - The gantry required about 20mm per side to be able to pass the tools.  To know how many tools you can fit it's simple math, measure that top bar -40mm to gantry and then divide the remainder by the size of your toolhead.

Once you have this add it all up and subtracked the length of your front extrusion.

Example: Voron 350 is 470mm total, 5 stealthburners is 76 x 5 = 380 -> 380 + 40 - 470 = 50, so that means you can fit 5 Stealthburners and have 50mm to spare which is not enoguh for any other tools.

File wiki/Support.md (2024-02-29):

1. [Methods](#methods)
2. [FAQs](#faqs)
3. [Build Guide](#build-guide)
4. [Macros](#macros)

## Methods

- For extra support join our [Discord](https://discord.gg/JhYY5BJe)
- For serial requests please see our [rules and how to](https://discord.gg/CjjZ4B5J)

## FAQs

1. After printing the parts make sure that the hex holes look to be proper hexes and that they are very uniform.  If they are misshapen chances are you need to reprint as you will have alignment issues.  It doesn't take much to be out by a lot.  Try printing at a slower speed if you have issues.

2. Calculating available size for tools (number of tools you can fit)
   - Dragon Burners require 60mm per tool (I recommend 5mm between for extruder handles)
   - Stealth Burners require 80mm per tool
   - The gantry required about 20mm per side to be able to pass the tools.  To know how many tools you can fit it's simple math, measure that top bar -40mm to gantry and then divide the remainder by the size of your toolhead.

3. Adjusting preload... Preload is created with the 2 countersunk screws in the tool plate.  These 2 screws need to be magnetic and will make contact with the magnets in the shuttle.  This adds 2 more wider points of contact at the base while also pre loading the sleeves/bearings.  To adjust them screw them all the way in, then slowly unscrew them 1/4 turn at a time (keeping each side even) until the tool no longer engages its self right away.  Once you reach a point where this happens, screw them back in 1/4 turn.  Each tool needs to be adjusted separately as printing irregularities can happen and this will allow you to compensate for it.  You may want to test and readjust these from time to time.

4. If you run homing on Z or QGL and you are getting lots of restarts or excessive runs.  Make sure you are using **N52** magnets, and check that your umbilicals are properly support and the right length.  If these 3 things aren't checked it will affect the tap precision.

5. A lot of people are asking which toolhead/extruder is recommended. The answer is whatever you want. The changer and tools are completely separate. That being said, using something that is already a tested combination for Stealth Burner or Dragon Burner is going to be the easiest.

6. CAN setup. You are definitely going to want to use CAN to connect your toolheads. Its only 4 wires and much lighter. You don't need anything fancy to split out the signal. Simple WAGO connectors work just fine. Of course, there are options for boards that will split the signal as well if you want something that looks a little more professional. Run wires up to the umbilical from your controller and power supply, then use WAGO's there to split the signal. See the guide here for a lot more CAN information: https://github.com/Esoterical/voron_canbus
   
7. If you try to change tools during a print (or when the hotends are active) and it drops off one tool, then waits behind another tool and does nothing, the issue is that its probably waiting for the tool temp to stabilize. Make sure you run a PID tune for each tool and place the info in the corresponding tool config.

## Build Guide
### Built on stream by [ZombieHedgehog](https://www.twitch.tv/zombiehedgehog)
| Episode | |
|--- |--- |
| 1 | https://youtu.be/YK2Zk2K584Y |
| 2 | https://youtu.be/yOGEAGLlvZc |
| 3 | https://youtu.be/W_r2b8U1J6k |
| 4 | https://youtu.be/cCbIjArKL4M |

## Macros

Tool_Align_Start - This macro will put the toolhead 100mm away from where you set the docking position. 
Tool_Align_Test - This macro will test the docking/undocking procedure. Start it from the docking position (start a few mm up on z, as the first movement is moving straight back on Y). 
Tool_Align_Done - This macro will move the toolhead back away from the dock.
A link to a video showing each one: [Youtube Video](https://www.youtube.com/watch?v=mOSi8zTpu_Q)

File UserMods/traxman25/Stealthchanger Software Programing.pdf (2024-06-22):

## Stealthchanger Software Programing

By: Traxman25
With parts and assistance from: Thessien
ComputerMedic
Klipper3d.org
Viesturz – Tap Changer project Frix-x – Shake Tune

You will need the following programs to complete this install: Raspberry Pi Imager (https://www.raspberrypi.com/software/) Notepad++ (https://notepad-plus-plus.org/downloads/)
WinSCP (https://winscp.net/eng/download.php)
Putty (https://www.chiark.greenend.org.uk/~sgtatham/putty/latest.html)

This guide is written for a Voron 2.4 350 Stealth Changer project with 6 tool heads. The hardware on this build is:
Raspberry Pi4B
Big Tree Tech Octopus v1.1 for the main drive motors
EBB36 tool head boards running either CanBus or USB communication For CanBus I used Big Tree Tech U2C
HDMI Screen
Big Tree Tech Filament Run Out Sensor V2.0
Orbiter V2.0 Extruders

The printer uses sensor less homing for X, and a Y switch moved into the A motor mount using this mod: https://github.com/VoronDesign/VoronUsers/tree/master/printer_mods/hartk1213/Voron2.4_Y_Endstop_Relocation (https://github.com/VoronDesign/VoronUsers/tree/master/printer_mods/hartk1213/Voron2.4_Y_Endstop_Relocation)

### Flashing Raspberry Pi firmware:

Raspberry Pi Imager (https://www.raspberrypi.com/software/)

Select your Raspberry Pi Device (Raspberry Pi 4)

Select the Operating System -> “Other Specific-purpose OS” -> 3D Printing -> Mainsail OS -> Mainsail OS

Choose Storage -> [choose the storage device you want to flash to]

Click Next - > Yes -> Yes. The installer will now write the Raspberry Pi firmware to the SD card.

Activating WiFi – On the flash drive will be a sample file called “wpa_supplicant.conf.example” Open this file in Notepad++ (You can not use Windows Notepad to generate this file) and follow the prompts for how to setup your specific wifi information.

Disconnect the flash drive

Insert the flash drive into the Raspberry Pi and power it on.

Note: If you have issues connecting the Pi via WiFi, connect via wired connection. Once the Klipper install is completed WiFi network details can be entered via the system settings in the Klipper Screen interface.

Once the Raspberry Pi is connected to your network log into it using Putty. (Host Name [name you gave the pi].local, or the IP address of the pi)

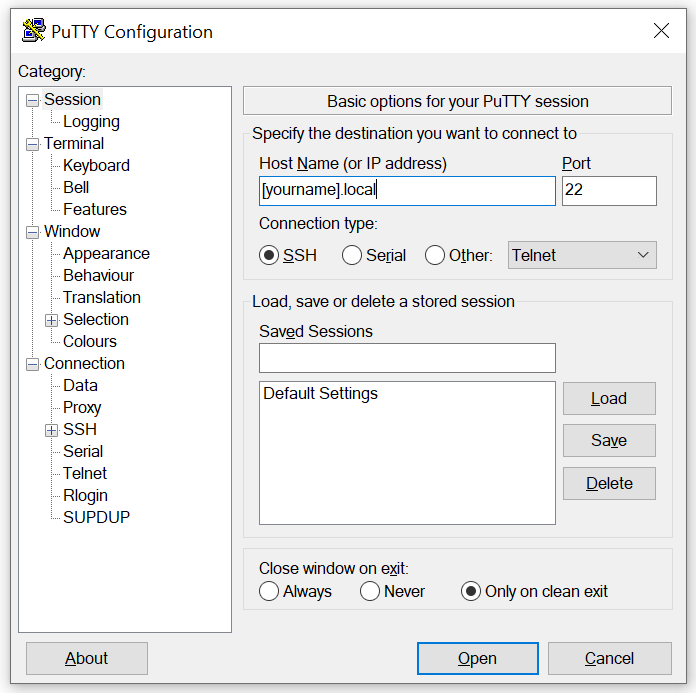
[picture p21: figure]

Enter the username and password you gave it while flashing the Pi OS.

Install git using the command:
sudo apt-get update && sudo apt-get install git

Install Kiauh using the command:
cd ~ && git clone https://github.com/dw-0/kiauh.git

Run Kiauh using the command:
./kiauh/kiauh.sh

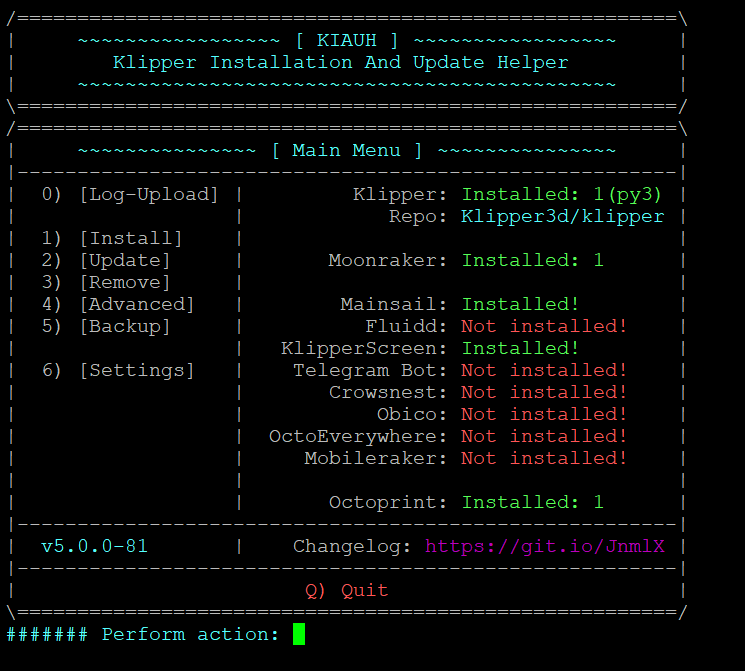
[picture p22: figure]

Press 1 enter to enter the Install menu

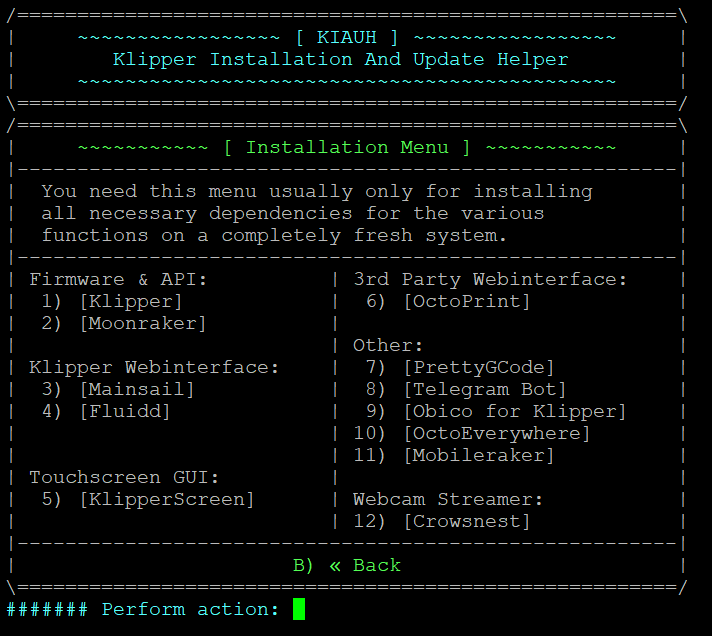
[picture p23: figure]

Install Klipper by entering 1 and following the prompts.

Complete the install by installing Moonraker, Mainsail or Fluid, KlipperScreen if you’re running a touch screen and any of the other optional applications that you’d like.

Once you’re done press B to go back.

### To flash the Firmware for the Octopus

Press 4 for Advanced

Press 2 for Build Only
Carefully setup the settings in the following menu according to the instructions for your control card:

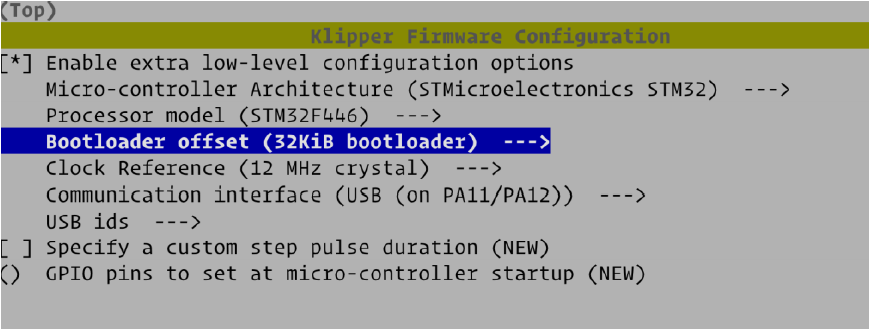
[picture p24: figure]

Press Q to Quit.

Press Y to write the Klipper.Bin file to the SD card.

Press B, then Q to quit.

Log into the pi with WinSCP.

Navigate to /home/(pi name)/klipper/out folder.

Either move the Klipper.Bin to the root folder of the flash drive, or download it to a folder you’ll remember.

Shut down the pi with the command sudo shutdown now

Remove the SD Card from the pi.

If you downloaded the Klipper.Bin file to your computer, connect the SD card to the computer and put the Klipper.Bin file onto the root directory of the SC card.

If you moved it using WinSCP you can put the flash drive directly into the control board.

Without the USB cable hooked to the pi, power up the control board. It will flash the firmware to the card in a few seconds.

Wait about a minute than power down the control card. To confirm the firmware was successfully flashed you can load the SD card and check that Klipper.Bin file name has been changed to Klipper.CUR

Reinsert the SD card into the Pi.

Hook up a USB cable from the USB A output on the Pi to the USB C input on the control card.

Boot up the pi and the control card.

ADXL RPi MCU install (Reference: https://www.klipper3d.org/RPi_microcontroller.html)

Install Raspberri Pi klipper MCU by entering the following command prompts
cd ~/klipper/
sudo cp ./scripts/klipper-mcu.service /etc/systemd/system/
sudo systemctl enable klipper-mcu.service

Make microcontroller code:
cd ~/klipper/
make menuconfig
Set “Microcontroller Architecture” to “Linux process” by pressing the down arrow to highlight Microcontroller Architecture, press the right arrow, down arrow down to Linnux process, press enter. Press Q
Press Y to save

Enter command prompt:

sudo service klipper stop
make flash
sudo service klipper start

Make sure the Linux SPI driver is enabled by running:
sudo raspi-config
and enabling SPI under the "Interfacing options" menu. (arrow down to option 3, right arrow to highlight <Select> hit Enter.

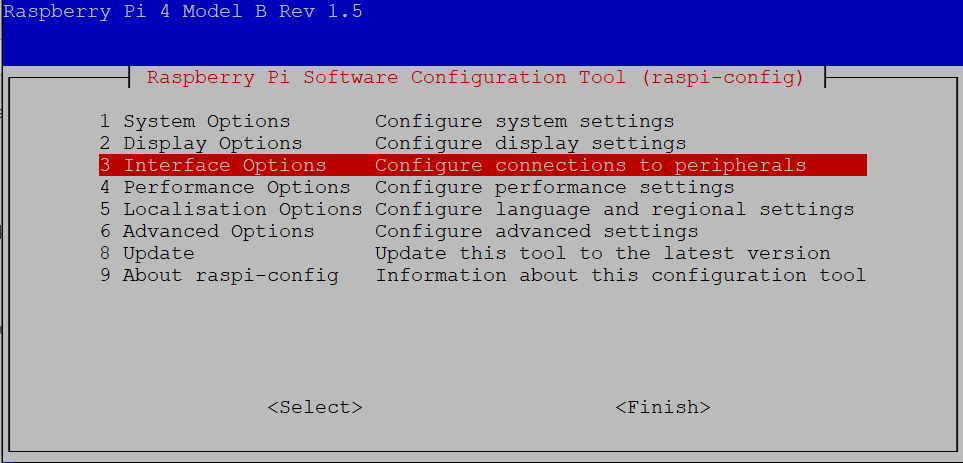
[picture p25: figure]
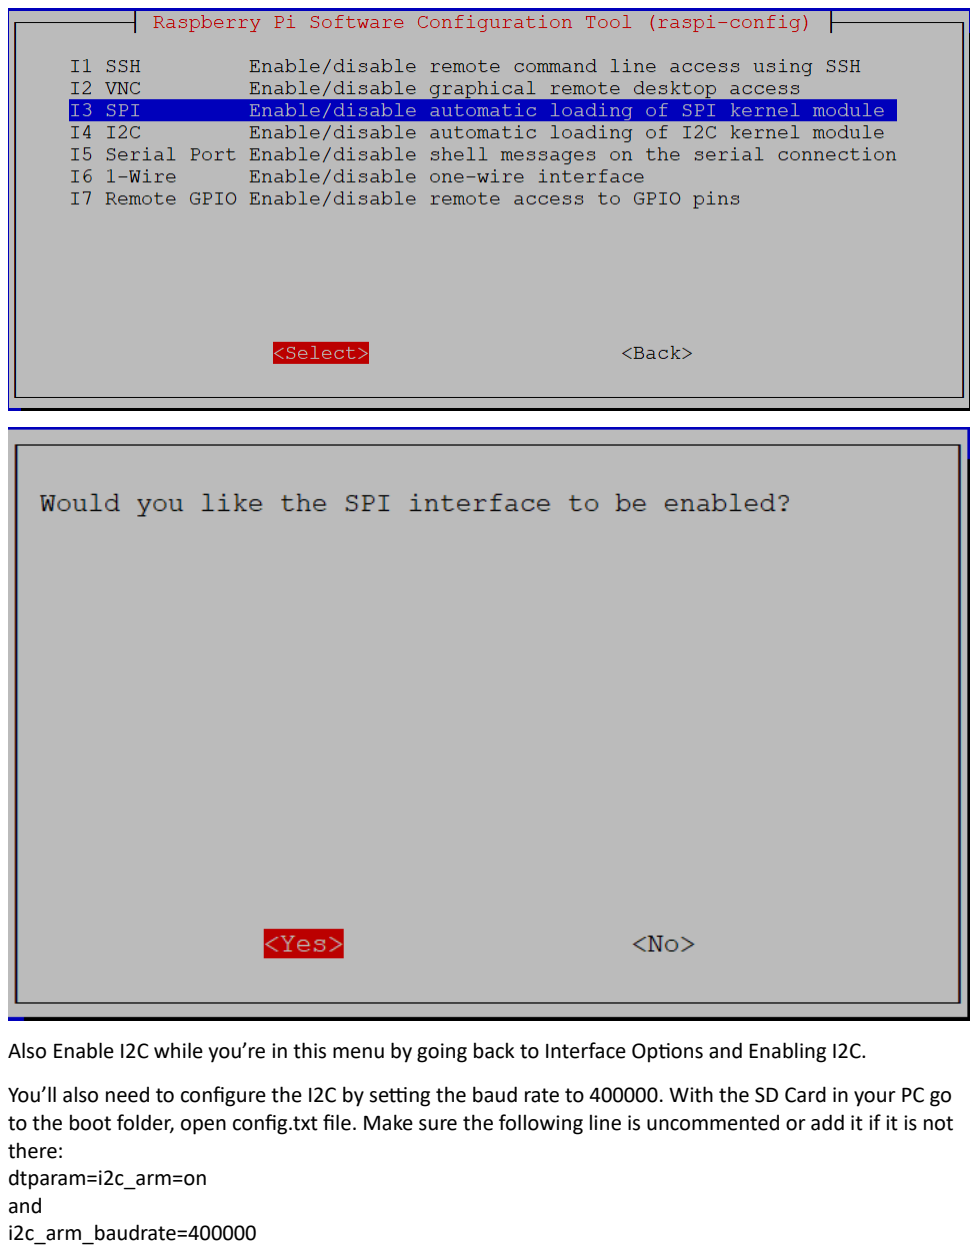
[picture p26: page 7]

Also Enable I2C while you’re in this menu by going back to Interface Options and Enabling I2C.

You’ll also need to configure the I2C by setting the baud rate to 400000. With the SD Card in your PC go to the boot folder, open config.txt file. Make sure the following line is uncommented or add it if it is not there:
dtparam=i2c_arm=on
and
i2c_arm_baudrate=400000

### Install Shaketune Input Shaper and Tuning Module (Reference: https://github.com/Frix-x/klippain-shaketune)

In putty enter command prompt:
wget -O - https://raw.githubusercontent.com/Frix-x/klippain-shaketune/main/install.sh | bash

(There is an additional step we will come back to later)

You should now have Klipper Screen working and be able to connect to the printer via a standard web interface. To log into the printer via a web browser you simple enter [printername].local or the IP address into your web browser address bar.

You will get an error message when connecting via the web browser, and on Klipper Screen. Ignore this for now.

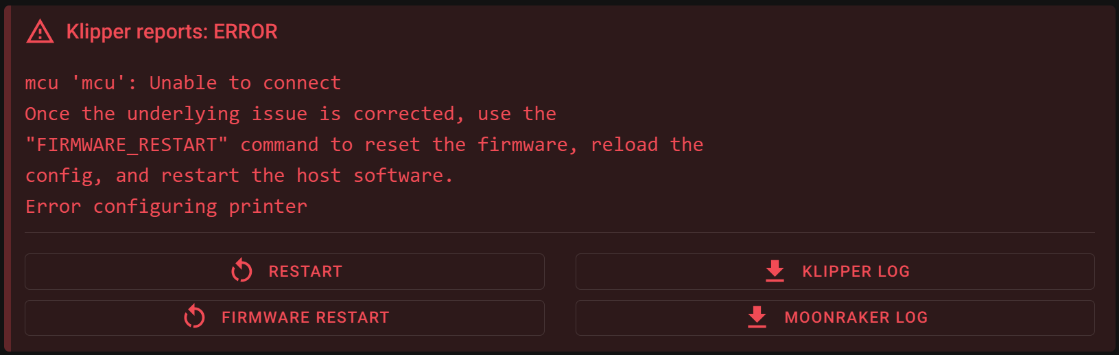
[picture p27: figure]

If you wish to connect via WiFi and had issues with that before, you can now go to Menu -> Network and select the network you wish to connect and enter the password.

On the Machine Tab, it is recommended to ensure all applications are up to date

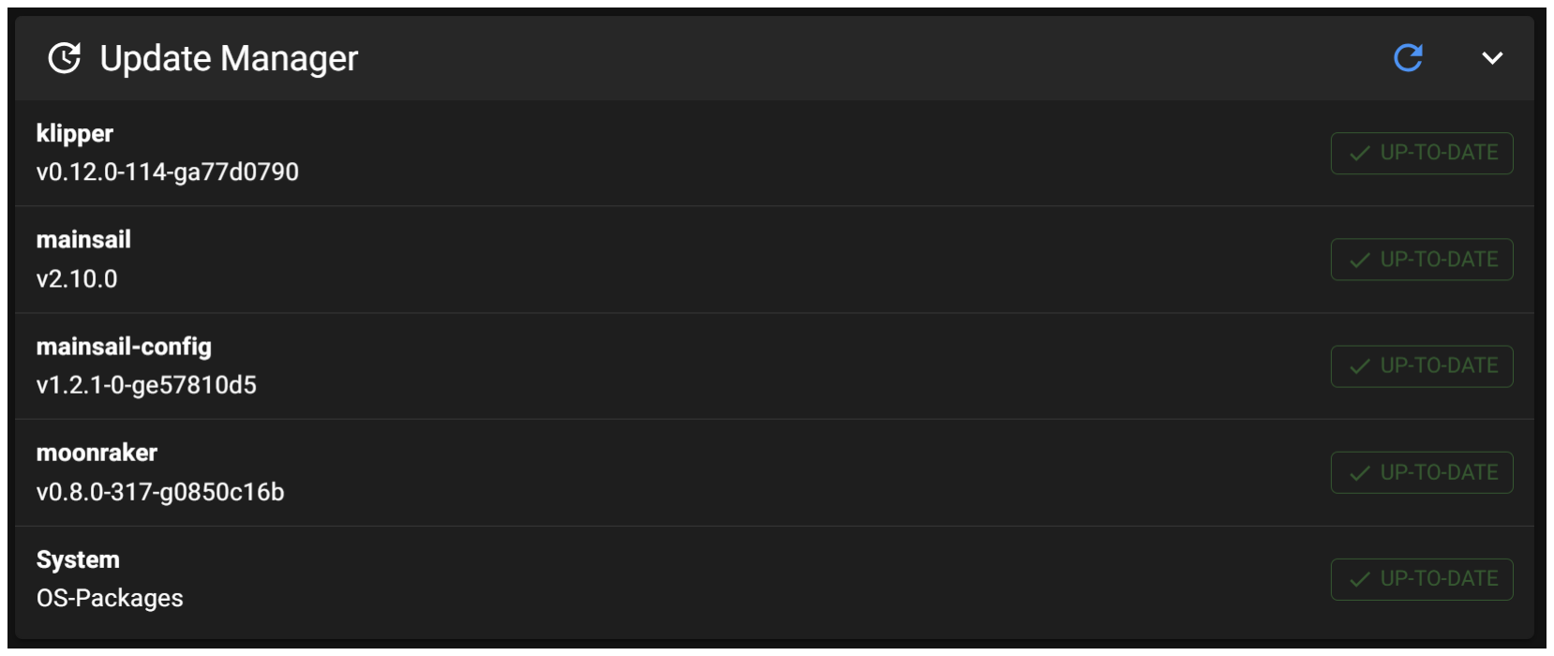
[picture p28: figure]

### ToolChanger Klipper Extension: https://github.com/viesturz/klipper-toolchanger

Run the following command in Putty:
wget -O - https://raw.githubusercontent.com/viesturz/klipper-toolchanger/main/install.sh | bash

Next to add toolchanger to the update section of Moonraker open moonraker.conf and add the following to the end of the file.
[update_manager klipper-toolchanger]
type: git_repo
channel: dev
path: ~/klipper-toolchanger
origin: https://github.com/viesturz/klipper-toolchanger.gitmanaged_services: klipper
primary_branch: main
install_script: install.sh
Also be sure to add the macros.cfg to your printer from the ToolChanger repo.

### Setting up printer.cfg

Starting with a stock Voron printer.cfg profile for your particular printer control board you’ll need to find the printer’s MCU ID. With the main printer control card plugged into the control computer, SSH into the controller and enter the command ls /dev/serial/by-id

This is your [mcu] serial address. Enter it after serial: /dev/serial/by-id/ as shown below.
Next is to include all of the sub configuration files. This allows settings and configurations to be located in separate files to help keep things manageable.

Below is a list of the files needed for a 6 tool changer. Homing.cfg is the custom homing override configuration. T0 through T5 is the configs for each individual tool head. Tool_detection.cfg is Also included is the config folder for ShakeTune.

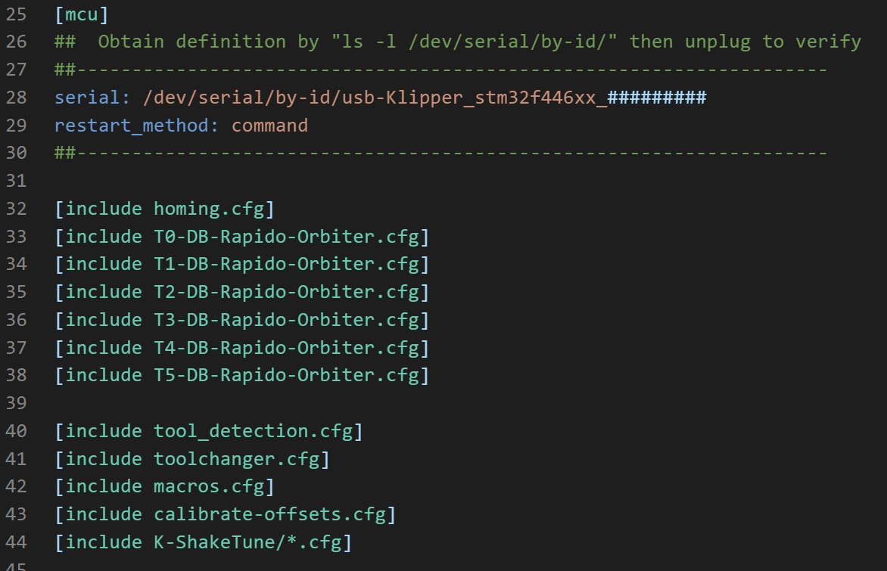
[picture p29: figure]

Add the [gcode_arcs], [rounded_path], and [excluding_object] sections as shown below.


If you’re using sensorless homing on x change the x endstop_pin to tmc2209_stepper_x:virtual_endstop

Also add driver_SGTHRS: 75 # 255 is most sensitive value, 0 is least sensitive below the stepper x section

Change Z endstop_pin to probe:z_virtual_endstop

Add the ADXL section shown below.


Add the [respond] and [force_move] sections as shown below

### Toolhead configs

Note: Tool head configs and pin addresses work a little differently with the tool changer. Tools are numbered starting a 0, so a 6 head tool changer would have tools 0 through 5.

Each tool head board is labeled by the mcu name that is given to it in the first line of the tool head board config file. Example shown below is tool 0 labeled et0 and tool 1 labeled et1. We’ll need this label as we build the pin callouts for each tool.

Each [function] section heading will need the tool head number after the label, except for on tool 0. Shown in the example below tool 0 extruder section is [extruder], tool 1 is [extruder1], etc.

Also each pin call out requires the tool head board name:pin# also shown in the example below. Example tool zero step_pin: et0:(pin#), tool 1 step_pin: et1:(pin#)

You’ll likely need to look up the pin numbers on the pin layout for the particular tool head board you’re using.

With the controller powered down hook up your tool head boards, boot up the controller, SSH into it and use ls /dev/serial/by-id to obtain all of the MCU IDs. Record the IDs that aren’t the main control board.

Download the toolhead sample config that matches your setup the closest from Viesturz tapchanger repo here: https://github.com/viesturz/tapchanger/tree/main/Klipper/config-example

If using Canbus for communication your MCU will be canbus_uuid: “ID number”
If using USB you will use the serial: “ID” style.

You’ll need to look up and enter your thermistor type.

It is easiest while setting up the printer to place the PID tune settings into the tool head config files rather than in the Save_Config in the main printer.cfg. This in case a tool head needs to be commented out then the Save_Config section does not need to be edited.


If you’re running headlight LEDs you’ll want to add the LED Control section into each tool head config Sequin LEDs usually use color_order: GRBW and have the initial_white: section

LED Sequins usually use color_order: GRB and do not use initial_white: section


The [tool T#] section contains the tool offset and park parameters for that tool.
Tool zero will have 0 for all gcode_offset values.

Params-type is the dock path type that is used during docking moves. We will address this a bit later

params_park_x y and z are where you will enter the physical location of that tool’s dock. As you’re setting up the config it is a good idea to enter an approximate location of the dock. Example your first dock will usually be X=25, Z close to the max z height of your printer. The next tools will be roughly +60mm in Y. We will fine tune these values later after initializing the printer and tuning z-offset.

Params_safe_y is the Y distance that is safe to for Z move up to the level of the docks.

Params_close_y is the Y distance that is save for x moves while moving from tool to tool, after dropping off a tool in it’s dock.

[tool_probe T#] is where you can adjust your probing samples, speed, retract distance, etc.
Pin is the pin number for the probe sensor
z-offset is that tools z-offset
speed is the downward z speed used during probing moves
Lift-speed is the upward z speed used to retract after the probe is triggered
samples is the number of probe samples taken at any given point
sample_retract_distance is the z height that the probe will raise between samples at a given point sample_tolerance is the allowable tolerance between probe measurements.
activate_code Heater=extruder(tool number unless zero) For tool zero leave the number off.

### toolchanger.cfg


Params_safe_y is the y distance that a loaded tool will safely clear the back of the parked tools. This will be used as the tools approach the dock from below.

Params_close_y is the y distance that is safe for an unloaded carriage to clear the back of docked tools. This will be used to move from dock to dock while changing tools. ***NOTE: The current sample config has this set to 15, please change it to at least 40 to prevent tools crashing. This is a global coordinate location, not an incremental move. So if you don’t change this the carriage will likely crash back into the tool after dropping it off.

Params_fast_speed is the rapid speed used during docking (mm/m). *** Note: It is recommended to turn this speed down to 1000 while tuning the docking moves. You can turn it back up once all the docks are tuned and proven to work. This speed is in mm/minute, divide by 60 for mm/s.

Params_path_speed is the slow speed used during docking and pickup moves. This speed is in mm/minute, divide by 60 for mm/s.

Params_type = ‘###’ Enter the tool path name to be used by your tool/dock combination. The path name is the params_(type)_path line below

### Printer Startup

Voron Designs has an excellent writeup for all the steps to initialize your new printer, available here: https://docs.vorondesign.com/build/startup/

Follow that guide to initialize your printer until you get to the Z-offset portion of the setup.

To set Z-offset, have tool 1 loaded onto the tool carriage. Home, quad gantry level and rehome the machine. Then move the print head to the center of the print bed. With a piece of paper on the bed plate carefully move the z axis down using the move commands until the nozzle causes a slight amount of drag on the paper. You should be able to push the paper under the nozzle. Also Be careful to not use a command that moves too far.

Note the z axis position and enter this as your z-offset position in that tools’ config file under the [tool_probe] - z_offset


Repeat these steps of hand loading each tool head you have to set the z-offset for each tool head. Be sure to run a quad gantry level and homing after swapping each tool head.

Once all of the z-offsets are complete use save and restart to restart Klipper.

### Dock Parking Location Alignment

Ensure that approximate park locations are setup in each tool’s config file.

Load Tool 0 onto the carriage, home, quad gantry level and rehome the printer.

Set the Speed factor to 50%

Run the Tool Align Start Macro – the tool head will move to the params_park_x and z values that are entered in that tool’s config. The tool head also move to 100mm more positive than params_park_y.

*Caution: Be sure to look from all directions to ensure the tool is not crashing during this step* Use the move commands to carefully move the tool into the dock. This location needs to be very precise so take your time to get the tool in just the right place. Most docking paths consider the parking location where the tool slides onto the pin/bolt. Example the hook-on dock park location is when the x and z locations line the head of the bolt up with the open hole in the tool face, and y location with the tool face against the dock.

Record the x, y and z location.

Tool Align Done will move the tool +100 y.

Move the tool to the center of the bed at Z=25mm.

Enter the X, Y and Z locations for the tool you just aligned into the params_park_x y and z in the tool config for that tool.

Save and Restart the printer.

Home, Quad Gantry Level and rehome with T0.

Set the speed to 50% or less.

Run TEST_TOOL_DOCKING to test the T0’s parking move path and parking location are correct.

Manually place the next tool onto the carriage.

Repeat these steps for all remaining tools.
Tool G-code offset alignment.

G-code offset alignment is to adjust for slight variations in each tool’s assembly, aligning all tools to each other for clean prints. No matter the method T0 should almost always have gcode_offsets for x, y and z at 0.

With any of the 3 methods outlined below take note of the offset for each tool and enter those offsets in the tool’s config file gcode_(axis)_offset setting.

Option 1: kTAMV - Klipper Tool Alignment (using) Machine Vision
kTAMV uses a small circuit board based web camera hooked up to your printer to look at each nozzle and measure the offset between T0 nozzle and the other tool’s nozzle. Instructions for kTAMV are available here: https://github.com/TypQxQ/kTAMV

Follow the steps there to get the offset measurements and take note of those offsets.

Option 2: NozzleAlign
NozzleAlign is a mostly 3D printed nozzle probe ball with a script to measure the nozzle position. More information and instructions are available here: https://github.com/viesturz/NozzleAlign?tab=readme-ov-file

Option 3: Print alignment prints
This method is to print test prints with T0 and each other tool. Then make adjustments to the gcode_offset values based on those prints and repeat the process.

Two options for test prints are available on Printables here: https://www.printables.com/model/109267-nozzle-alignment-assisthttps://www.printables.com/model/201707-x-y-and-z-calibration-tool-for-idex-dual-extruder-

A test print of stacked cubes will help ensure all of the nozzles are aligned.

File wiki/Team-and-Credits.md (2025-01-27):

1. [Official Team Roster](#official-team-roster)
2. [Credits](#credits)

# Official Team Roster

## Core Team

| Github 	| Discord 	| Main Role |
|---	|---	|--- |
| [BT123D](https://github.com/bt123d/) | bt123_ | Designer |
| [Hellsparks](https://github.com/Hellsparks/) | _hellspark | Designer |
| [jdmontgomer](https://github.com/jdmontgomer/) | jdmontgomery | Tester/PR |
| [TheSin-](https://github.com/thesin-/) | thessien | Designer |
| | | |

## Extended Team

| Github 	| Discord 	| Main Role |
|---	|---	|--- |
| [BrewNinja](https://github.com/BrewNinja/) | BrewNinja | Tester/Documentation |
| [MikeYankeeOscarBeta](https://github.com/MikeYankeeOscarBeta/) | dubiousmnemonic | Tester |
| [N3MI-DG](https://github.com/N3MI-DG/) | N3MI | Tester |
| [nic335](https://github.com/nic335/) | nic335 | Tester |
| [traxman25](https://github.com/traxman25/) | Traxman25 | Tester |
| | | |

## Former Members

| Github 	| Discord 	| Main Role |
|---	|---	|--- |
| [fiferboy](https://github.com/fiferboy/) | fiferboy | Designer |
| [ostroma](https://github.com/ostroma/) | nobo6855 | Tester |
| | | |

## Special Mentions

* Testing the LDO parts (Discord names): arthurledaron, broncosis, dudewithan02, dweenz., fr0stbyt3, gmbridge, hartk, rferrington783, theaninova
* Contributors see the [Usermods](https://github.com/DraftShift/StealthChanger/tree/main/UserMods) folders.

# Credits

* [VoronDesign](https://github.com/VoronDesign)
* [Micron](https://github.com/PrintersForAnts/Micron)
* [TapChanger](https://github.com/viesturz/tapchanger) by Viestures
* [Dragon/RapidBurner/Yavoth](https://github.com/chirpy2605/voron/tree/main/V0/Dragon_Burner) by Chirpy
* [Archetype](https://github.com/Armchair-Heavy-Industries/Archetype/tree/main) by Leddy/Armchair Heavy Industries
* [Xol](https://github.com/Armchair-Heavy-Industries/Xol-Toolhead) Maintained by DW-Tas/Armchair Heavy Industries
* [Anthead](https://github.com/PrintersForAnts/AntHead) by hartk (Printers for Ants)

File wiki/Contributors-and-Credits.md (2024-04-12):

| Github 	| Discord 	| Main Role |
|---	|---	|--- |
| [Hellsparks](https://github.com/Hellsparks/) | _hellspark | Designer |
| [TheSin-](https://github.com/thesin-/) | thessien | Designer |
| [BT123D](https://github.com/bt123d/) | bt123_ | Designer |
| [fiferboy](https://github.com/fiferboy/) | fiferboy | Designer |
| [paeppi88](https://github.com/paeppi88/) | paeppi88 | Contributor |
| [MarcO](https://github.com/ostroma/) | MarcO | Tester |
| [BrewNinja](https://github.com/BrewNinja/) | BrewNinja | Documentation |

* For other Contributors see the [Usermods](https://github.com/DraftShift/StealthChanger/tree/main/UserMods) folders.

Credits

* [VoronDesign](https://github.com/VoronDesign)
* [TapChanger](https://github.com/viesturz/tapchanger) by Viestures
* [Dragon/RapidBurner](https://github.com/chirpy2605/voron/tree/main/V0/Dragon_Burner) by Chirpy
* [Archetype](https://github.com/Armchair-Heavy-Industries/Archetype/tree/main) by Leddy/Armchair Heavy Industries
* [Xol](https://github.com/Armchair-Heavy-Industries/Xol-Toolhead) Maintained by DW-Tas/Armchair Heavy Industries

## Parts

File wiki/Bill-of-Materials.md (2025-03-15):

All parts (screws, magnets, etc) are Voron, and Voron Tap standards.

1. [Shuttle](#shuttle)
2. [BackPlates](#backplates)
3. [Endstops](#endstops)
4. [Options](#options)
5. [Sexball Probe](#sexball-probe)
6. [Affiliate Links](#affiliate-links)

## Shuttle

- [3] 6x3mm magnets (N52 Highly recommended to counter the pull from the umbilicals)
- [2] m3x6 BHCS (tap sensor)
- [4] m3x6 BHCS head (mgn bolts) `m3x12 if used with the shuttle keeper`
- [3] 4x6x6mm brass bushing (4mm id x 6mm od x 6mm tall)
- [2] m3x40 SHCS (Optional: to stiffen the shuttle, **Fully threaded, no shoulder**)

## Backplates

x1 per toolhead

### All Tools

**Note:** heatsets on the SB version in from the opposite side as the Voron instructions, slightly longer screws on the CW2 attachment may be required

- [4] m3 heat inserts
- [3] Ø4x12mm ssRod (dowel pin) with a rounded end **(if it has female threads on the back it will be listed as an M3, but make sure the pin is 4mm OD, that is what is important. We recommend the threaded pins for better fixing)**
- [1] 6x3mm magnet (N52 Highly recommended to counter the pull from the umbilicals. Note that most magnets not from a reputable source may say N52 but aren't actually. Recommend one of the two links below.)
- [2] m3x6 or m3x8 FHCS (Flat head countersunk screw, MUST BE MAGNETIC. no stainless, as per TAP)
- [1] [OptoTap](https://s.click.aliexpress.com/e/_DEGsGTV) (only the sensor PCB is required)
- [1] m3x8 BHCS (optional in v1.1)

**The list bellow is in addition to the Stealthburner BOM above.**

### Dragonburner/Rapidburner/Yavoth

- [1] m3x12 BHCS (optional to keep spacer in place)
- [2] m3x35 SHCS
- [2] m3 heat inserts
- [2] m3x8 BHCS (optional in v1.1)

**Note:** Dragonburner [extended mount](https://github.com/chirpy2605/voron/tree/main/general/Alternative_Voron_Mounts/Extended_Extruder_Mounts) is required depending on extruder

### Archetype Blackbird

- [1] m3x12 BHCS (to hold the sherpa mount in place)
- [2] m3 heat inserts
- [2] m3x8 BHCS (optional in v1.1)

### Xol

- [2] m3x6 BHCS (backplate lower mounting screws. m3x8 will be too long)
- [2] m3x20 BHCS (backplate upper mounting screws)
- [2] m3x8 BHCS (extruder mount to backplate)
- [2] m3x6 FHCS **magnetic** (preload screws. m3x8 will be too long)
- You will **not be able** to use stock 2.4 Z joints with Xol or A4T.
- Replacement of your Z joints with something with a lower profile such as [hartk123's GE5C Z Joint](https://github.com/VoronDesign/VoronUsers/tree/main/printer_mods/hartk1213/Voron2.4_GE5C) or [Ellis'Short Z Joints](https://github.com/VoronDesign/VoronUsers/tree/main/printer_mods/Ellis/Short_Z_Joints) is necessary to avoid bottoming out your Z carriage on the deck panel when using Xol or A4T.

### A4T

- [2] m3x45 SHCS **magnetic** (backplate lower mounting screws)
- [2] m3x12 BHCS / SHCS (backplate upper mounting screws)
- [2] m3x6 FHCS **magnetic** (preload screws. m3x8 will be too long)
- You will **not be able** to use stock 2.4 Z joints with Xol or A4T. See links in Xol section above for links to alternative suggestions.

## Endstops

Optional

- [1] m3x6 BHCS
- [1] m3 heat insert
- [1] 6x3mm magnet (Hall Effect Sensor ONLY, Voron spec)

## Options

You will likely need help with belts, make sure to decide on if you will use the [shuttle keeper](https://github.com/DraftShift/Stealthchanger/tree/main/STLs/Extras) or use the [belt helper](https://github.com/DraftShift/Stealthchanger/tree/main/STLs/Extras/BeltHelper).  And print the required parts and make sure to have the addition bill of materials for them.

## Sexball probe

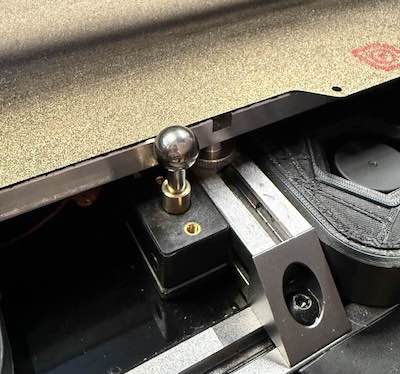
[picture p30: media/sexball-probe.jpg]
Sexball probe


Image By asoli

Calibration probe option that just replaces the shaft on a sexbolt.
- [Probe](https://s.click.aliexpress.com/e/_oB1egOH)
- [12mm Ball with M5 Threads](https://s.click.aliexpress.com/e/_o2DGfvf)
- [M5x30mm External Thread Pin](https://s.click.aliexpress.com/e/_omw2qxX)

**NOTE:** For micron M5x25mm Pin is tall enough

**NOTE:** Only use the hartk style bodys with the sleeves, knockoffs have too much slop.

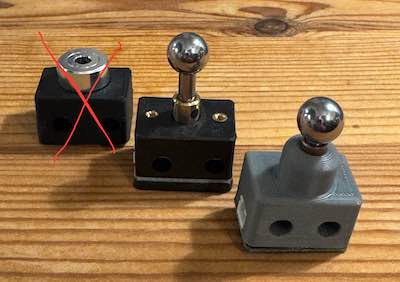
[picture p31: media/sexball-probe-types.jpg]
Sexball probe types


Image by BT123

## Affiliate Links

| Parts 	  | Link 1 | Link 2 | Link 3 |
|---  |---|---|---|
| Bushing 	  | [AliExpress](https://s.click.aliexpress.com/e/_Dmsh3LJ) | [US Amazon](https://amzn.to/3RAjKtY) | [UK Amazon](https://amzn.to/48jnoPO) | 
| Pin 	  | [AliExpress](https://s.click.aliexpress.com/e/_DCQkrFP) | [US Amazon](https://amzn.to/3GZBSZn) | [UK Amazon](https://amzn.to/488gP2v) |
| N52 Magnets | [US KB-3D](https://kb-3d.com/store/magnets-bearings/995-disccylinder-magnet-high-temp-n52h-6x3mm-1696789934996.html) | [UK Printy Please](https://www.printyplease.uk/N52H) | |

Due to QC issues, this is an [Alternative bush](https://s.click.aliexpress.com/e/_DFJQgtN) which has also been tested and works fine.

Alternatively you can purchase check on our official [vendors list](Vendors-and-Kits)

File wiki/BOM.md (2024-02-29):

# Bill of Materials

All parts (screws, magnets, etc) are Voron, and Voron Tap standards.

1. [Shuttle](#shuttle)
2. [BackPlates](#backplates)
3. [Endstops](#endstops)
4. [Links](#links)

## Shuttle

- [3] 6x3mm magnets (N52 Highly recommended to counter the pull from the umbilicals)
- [2] m3x6 BHCS (tap sensor)
- [4] m3x6 BHCS head (mgn bolts)
- [3] 4x6x6mm brass bushing (4mm id x 6mm od x 6mm tall)
- [2] m3x40 SHCS (Optional: to stiffen the shuttle)

## Backplates

x1 per toolhead

### Stealthburner

**Note: heatsets on the SB version in from the opposite side as the Voron instructions, slightly longer screws on the CW2 attachment may be required**

- [4] m3 heat inserts
- [3] Ø4x12mm ssRod (dowel pin) with a rounded end **(if it has female threads on the back it will be listed as an M3, but make sure the pin is 4mm OD, that is what is important)**
- [1] 6x3mm magnets (N52 Highly recommended to counter the pull from the umbilicals)
- [2] m3x6 or m3x8 FHCS (Flat head countersunk screw, MUST BE MAGNETIC. no stainless, as per TAP)

### Dragonburner

- [1] m3x12 BHCS (optional to keep spacer in place)
- [2] m3x35 SHCS
- [2] m3 heat inserts
** Note: Dragonburner extended mount is require depending on extruder**

## Endstops

Optional

- [1] m3x6 BHCS
- [1] m3 heat inserts
- [1] 6x3mm magnet (Hall Effect Sensor ONLY, Voron spec)

## Links

**note links are affiliates**

| Parts 	| Link 1 UK Amazon 	| Link 2 AliExpress 	| Link 3 US Amazon	  | Link 4 	|
|---	|---	|---	|--- |---	|
| Bushing 	| https://amzn.to/48jnoPO 	| https://s.click.aliexpress.com/e/_Dkek3Op | https://amzn.to/3RAjKtY | 	|
| Pin 	| https://amzn.to/488gP2v 	| https://s.click.aliexpress.com/e/_DEfc0JB	| https://amzn.to/3GZBSZn | 	|

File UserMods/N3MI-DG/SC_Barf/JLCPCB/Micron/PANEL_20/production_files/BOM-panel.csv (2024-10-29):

Comment | Designator | Footprint | LCSC | Quantity
100nF | C1,C2,C3 | C_0402_1005Metric | C14445 | 3
470R | R1 | R_0402_1005Metric | C25117 | 1
SK6805-EC15 | D1,D10,D11,D12,D13,D14,D15,D16,D17,D18,D19,D2,D3,D4,D5,D6,D7,D8,D9 | SK6805-EC15 | C2890035 | 19

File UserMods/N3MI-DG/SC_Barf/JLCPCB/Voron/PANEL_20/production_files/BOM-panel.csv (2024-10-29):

Comment | Designator | Footprint | LCSC | Quantity
100nF | C1,C2,C3 | C_0402_1005Metric | C14445 | 3
470R | R1 | R_0402_1005Metric | C25117 | 1
SK6805-EC15 | D1,D10,D11,D12,D13,D14,D15,D16,D17,D18,D19,D2,D20,D21,D3,D4,D5,D6,D7,D8,D9 | SK6805-EC15 | C2890035 | 21
Conn_02x03_Counter_Clockwise | J1 | PinHeader_2x03_P2.54mm_Vertical_SMD |  | 1

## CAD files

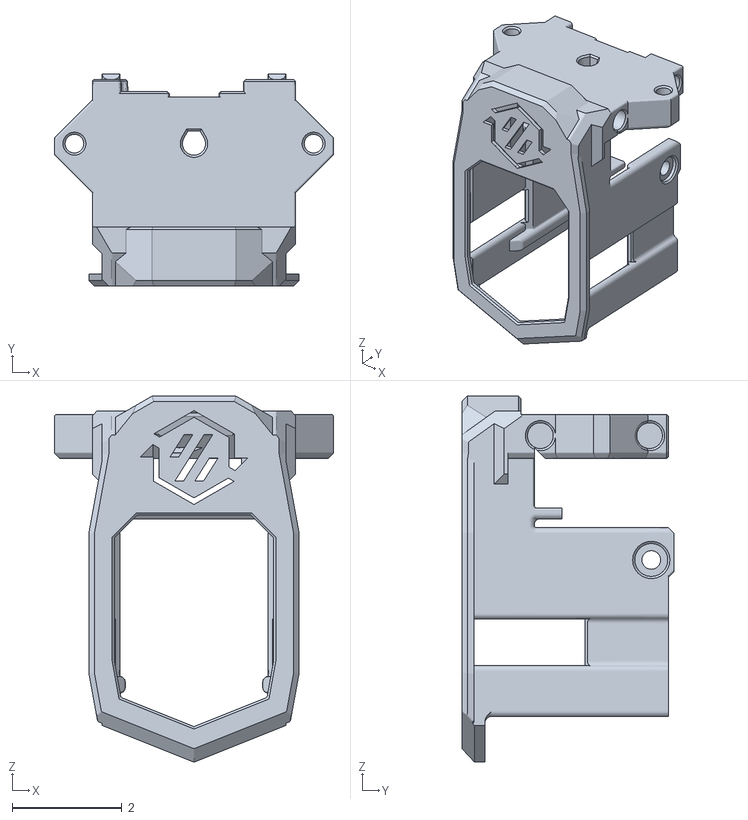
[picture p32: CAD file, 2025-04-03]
UserMods/BrewNinja/Anthead/CAD/N3MI_Anthead_Main_Body_Voron_Sherpa_Relaxed.obj
5.08 x 3.86 x 6.66

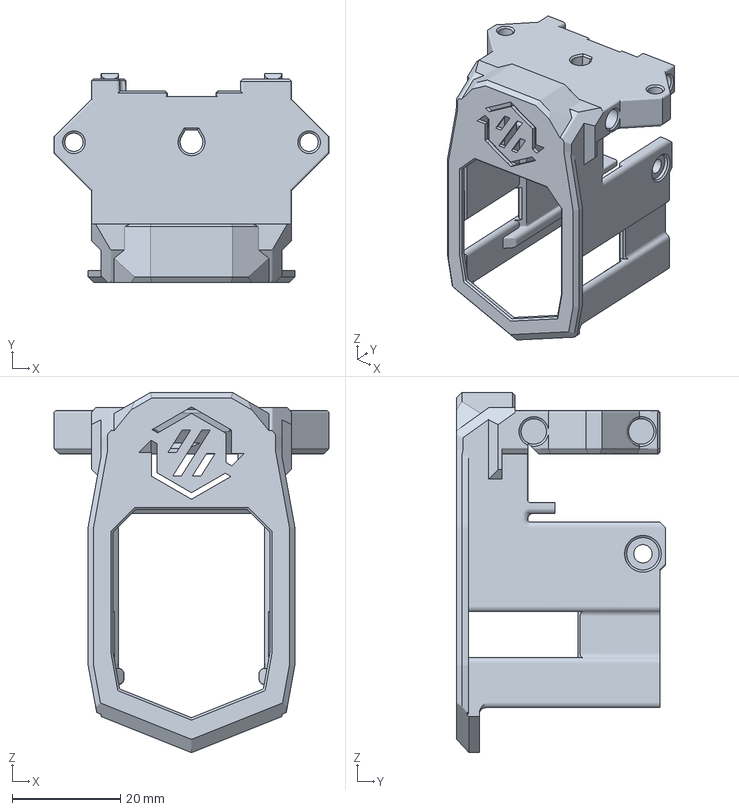
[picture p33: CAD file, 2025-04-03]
UserMods/BrewNinja/Anthead/Files/N3MI_Anthead_Main_Body_Voron_Sherpa_No_Supports_Relaxed.3mf
50.8 x 38.6 x 66.6 mm

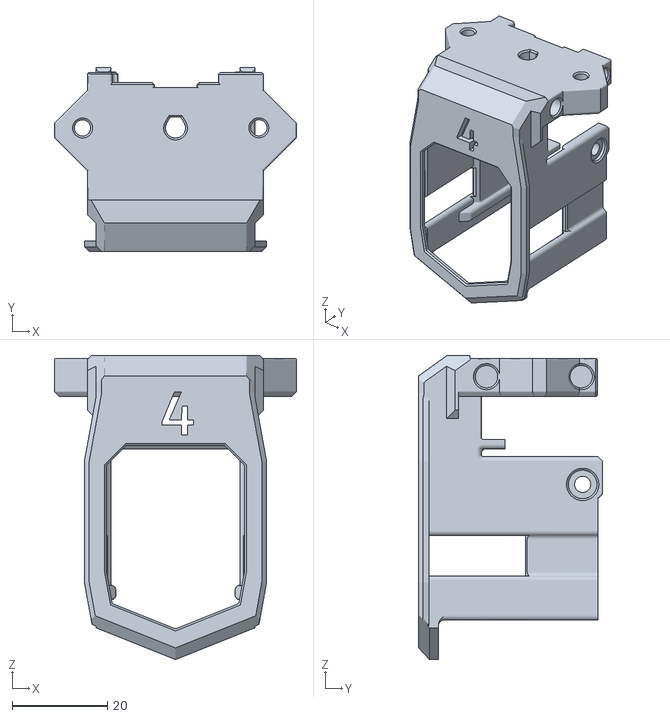
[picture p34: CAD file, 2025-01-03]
UserMods/traxman25/Ant Head/ant head main body 4.STL
50.8 x 38.6 x 63.8

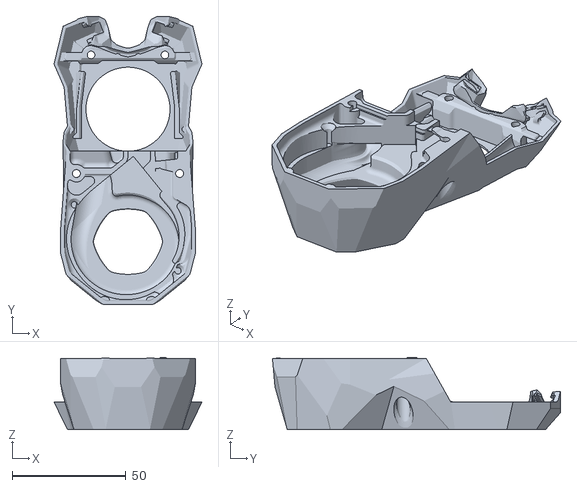
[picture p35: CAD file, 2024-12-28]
UserMods/N3MI-DG/StealthBurner_SC_Barf/STL/[a]_stealthburner_main_body.stl
65.1 x 126.8 x 31.8

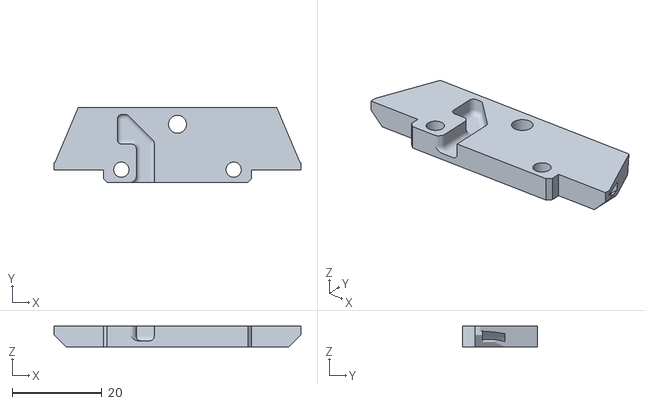
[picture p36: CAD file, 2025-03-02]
STLs/Backplates/Anthead_Spacer_Full.stl
55.0 x 16.6 x 4.56

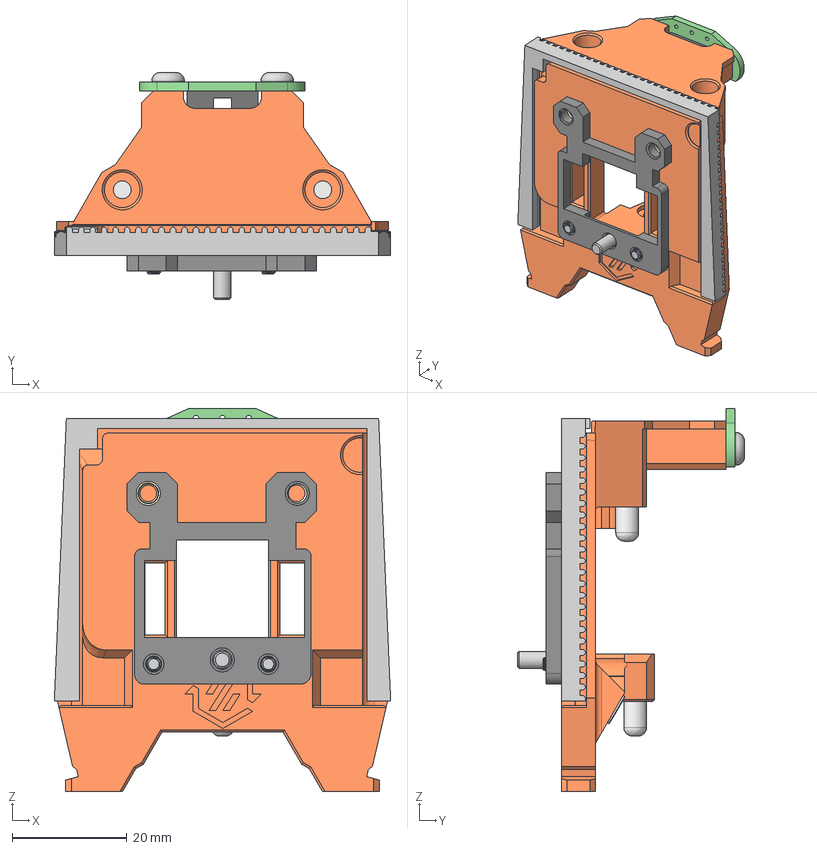
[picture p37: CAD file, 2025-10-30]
CAD/Backplates/JabberWocky.step
58.7 x 39.6 x 66.8 mm
Board
Sensor
M3x6 BHCS (2) x 2
M3x6 FHCS (7) (1)
M3x6 FHCS (7) (1) (1)
Pins 4x12 Rounded
3x6mm Magnet (1) (3) (2) (1)
M3 Threaded Insert (3) x 2
Pins 4x12 Rounded (1)
Pins 4x12 Rounded (2)
M3x6 BHCS
91290A101_Alloy Steel Socket Head Screw x 2
Supports
Spacer (1)

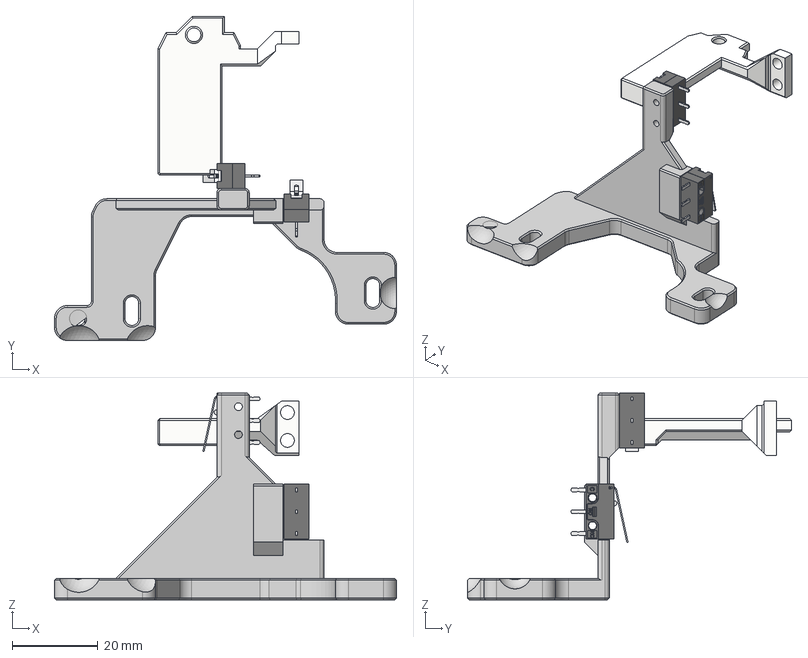
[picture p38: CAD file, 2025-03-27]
CAD/Switch_Endstop.step
79.6 x 75.4 x 48.1 mm
[a]_switch_bracket
[a]_switch_arm
Switch Body x 2
Lever x 2
Contacts x 2
Plunger x 2

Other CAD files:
UserMods/BrewNinja/Anthead/CAD/N3MI_Anthead_Main_Body_Voron_Sherpa.obj
UserMods/BrewNinja/Anthead/Files/N3MI_Anthead_Main_Body_Voron_Sherpa_No_Supports.3mf
UserMods/traxman25/Ant Head/ant head main body 0.STL
UserMods/N3MI-DG/Anthead_Mods/STL/Main_Body_Voron_Sherpa.stl
UserMods/traxman25/Ant Head/ant head main body 3.STL
UserMods/N3MI-DG/Anthead_Mods/STL/Main_Body_Voron_O2.stl
UserMods/N3MI-DG/Anthead_Mods/STL/Main_Body_Micron_O2.stl
UserMods/traxman25/Ant Head/ant head main body 1.STL
UserMods/traxman25/Ant Head/ant head main body 5.STL
UserMods/N3MI-DG/Anthead_Mods/STL/Main_Body_Micron_Sherpa.stl
UserMods/traxman25/Ant Head/ant head main body 2.STL
CAD/Backplates/A4T.step
CAD/Backplates/Anthead.step
CAD/Backplates/BlackBird.step
CAD/Backplates/DragonBurner.step
CAD/Backplates/DragonBurner_Legacy.step
CAD/Backplates/RapidBurner.step
CAD/Backplates/RapidBurner_Legacy.step
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

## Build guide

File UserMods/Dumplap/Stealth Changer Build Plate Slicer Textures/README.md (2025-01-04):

# Slicer Build Plate Textures with StealthChanger & Micron

|Micron Plate|StealthChanger Plate|
|:---:|:---:|
|[](Plates/Micron%20SC%20Plate%20180x180.svg)|[](Plates/)|
|**sizes**|**sizes**|
|180x180|120x120 <br><br> 180x180 <br><br> 255x185 <br><br> 255x255 <br><br> 305x235 <br><br> 305x305 <br><br> 355x285 <br><br> 355x255 <br><br> 370x377|
<br>
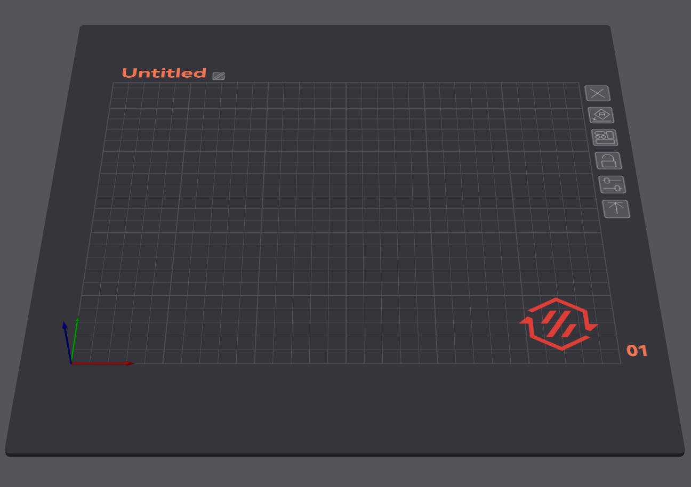
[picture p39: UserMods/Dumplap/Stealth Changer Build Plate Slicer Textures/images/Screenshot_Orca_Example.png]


## [Custom Build Plate Size?](Custom%20Build%20Plates/)

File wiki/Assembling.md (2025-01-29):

1. [Assembling Shuttle and Backplates](#assembling-shuttle-and-backplates)
2. [Preload](#preload)
4. [Tips and Tricks](#tips-and-tricks)

**NOTE: Currently pins may feel very loose, this is by design to allow for room for glue or epoxy (recommended) to set.  Normally press fit is good enough for testined, but for actual use make sure to secure the pins properly.**

**NOTE: D2HW shuttle is not compatible with Hall Effects, and D2HW back plate will affect cooling.**

## Assembling Shuttle and Backplates

In order to get proper matching set you should:
- insert pins in your best backplate (straightest)
- press bushings in the shuttle and ensure a smooth mating between the parts.
- inset 2x M3x8mm SHCS screws in the top 2 pins to secure, and a M3x6 or 8mm BHCS screw in the bottom pin. The StealthBurner back plate needs the pins glued so this is done as the last step
- if everything feels smooth, so pop the bushings out and glue them in place using either superglue or epoxy, other wise see [Heat Treating](#heat-treating)
- be sure to test that the mating still feels smooth after the glue sets.
- You can now use the shuttle as a "master blank" for glueing the pins into all your backplates.

## Preload

**NOTE** Every backplate needs to be adjusted.

Preload is meant remove all the wiggle when it's fully seated by preloading the pins onto the bushings.

To set your preload you want to back the FSCS screws till they are just touching the magnest on the shuttle.  See [Preload Paper Trick](#preload-paper-trick)

## Tips and Tricks

### Heat Treating

If you printed the shuttle and backplate and things are just not smooth or you have slight binding, you can Heat Treat it and here is how.
- Fully assemble the shuttle and backplate with Bushing, Pins, Screws and Magnets
- Set your heat bed to 100-110°C
- Once at temperature, mate both parts fully, and set them on the bed with the backplate (tool side) down
- After 20+ minutes pick them up and slide them 3-4 times, then fully mate them once again
- With both parts still fully mated, set them down with the backplate (tool side) down someplace flat and at room temperature and let them fully cool without touching them for 5+ hours
- Try and slide them again and you should feel an improvement, you can try this multiple times if you are still not satisfied

Big thank you to `unguided-wanderer` on Discord for this technique.

### Preload Paper Trick

You can use a piece of paper per side to make sure they both have the same pressure.

Big thank you to `ButtSlark` on Discord for this technique.

### Cleaning out bushings

Sometimes the bushings aren't debured or do not slide well when you recieve them.

Bushing Cleaning (https://www.youtube.com/watch?v=AHlydBsMJro)

- Find a drill bit 4mm or smaller (I’m using 3mm in the video at the link)
- Using your thumb, apply pressure onto the bush and roll back and forth on the drill bit. 
- Test on the pin again
- Rinse and repeat. 

Some bushings take multiple tries, but try not to over do it, just enough that the bushing falls on the pin.

Big thank you to `BT123` on Discord for this technique.

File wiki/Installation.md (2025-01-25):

All sections are required, so please follow all steps carefully.

1. [Klipper Addon](#klipper-addon)
2. [Toolchanger Configuration](#toolchanger-configuration)

**NOTE:** DangerKlipper is not currently supported

**NOTE:** Your klipper version eneds to be newer than Jun 14, 2024 (1591a51)

**NOTE:** Before you start remove your `PRINT_START` and `PRINT_END` macros out of the config as toolchanging requires a specific version of these to initialize and start printing.

## Klipper Addon

You must install [klipper-toolchanger](https://github.com/viesturz/klipper-toolchanger/), Follow instruction on the linked page.

## Toolchanger Configuration

You need `homing.cfg`, `macros.cfg`, `tool_detection.cfg` and `toolchanger.cfg` from [TapChanger Example](https://github.com/viesturz/tapchanger/tree/a277492516af3751aa13f5097a908ab8a88b6eae/Klipper/config-example)

`homing.cfg` assumes you are using sensorless for X axis and a physical switch for Y axis.  It's important to use this file when building your own homing as the order and macros it calls are required.  If you use Hall Effects or switch end stops for both Axis, remove the `_SENSORLESS_HOME_X` call in `[homing_override]` with `G28 X`.  Alternatively if you use sensorless for both you need so update `G28 Y` to use a copy of `_SENSORLESS_HOME_X` but for Y. There is a second place in the homing override that sets your Y rebound.  The default is 20, without keeper you likely want this around 4-5, change `G0 Y{ max_y - 20 } F5000` to `G0 Y{ max_y - 5 } F5000` notice the 20 that changes.  This is something you may need to adjust to figure out the position of your switch.

**NOTE:** when using sensorless Y make sure that the `homing_retract_dist` in the `[stepper_y]` section is set to 0 as per [Voron Docs](https://docs.vorondesign.com/community/howto/clee/sensorless_xy_homing.html)

You can either add them manually to your klipper install, or alternatively, you can integrate them to your config so that moonraker keeps them up to date with your other software if they change. Below are the steps for the integrated way. If you make any changes to the files though, they will be overwritten if you update. If you choose to manually add them, make sure your printer.cfg reflects the location of them.

**On the Klipper System** 
```
cd ~
git clone https://github.com/viesturz/tapchanger.git --no-checkout --depth 1 --filter=blob:none
cd tapchanger
git sparse-checkout init --cone
git sparse-checkout set Klipper
git checkout
cd ~
ln -s ~/tapchanger/Klipper/config-example ~/printer_data/config/tapchanger
```

**Add to moonraker.conf**
```
[update_manager tapchanger]
type: git_repo
path: ~/tapchanger
origin: https://github.com/viesturz/tapchanger.git
primary_branch: main
managed_services: klipper
```

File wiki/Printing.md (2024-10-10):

1. [Parts](#parts)
2. [Settings](#settings)
3. [Orientation](#orientation)

## Parts

**NOTE: If you plan on using the Tapchanger Dragonburner dock you must use the [custom cowl by OstroMa](https://github.com/DraftShift/StealthChanger/blob/main/UserMods/OstroMa/DB_Cowl_v8_with_TapChanger_Dock_Hooks.stl). We always recommend to use the original cowls when possible and the [Modular Dock](https://github.com/DraftShift/ModularDock) does not require any special Cowl, print the original from the Dragonburner repo.**

Coming Soon

## Settings

All print settings are the same as [Voron Standards](https://docs.vorondesign.com/sourcing.html#print-settings) or better.

Since every filament shrinks at a different rate and our tolerances are too tight to allow for "pre-scalling".  You need to calibrate the shrinkage for each and every filament you use, even the same brand but different colour can shrink at a different rate.  We recommend using Califlower for each filament.

- Shuttle is the only part that requires supports and should be set to `touching build plate`

## Orientation

Print orientation is flat on the parts back with supports enabled currently, we are working on models with integrated supports.

- All stls are in the proper print orientation

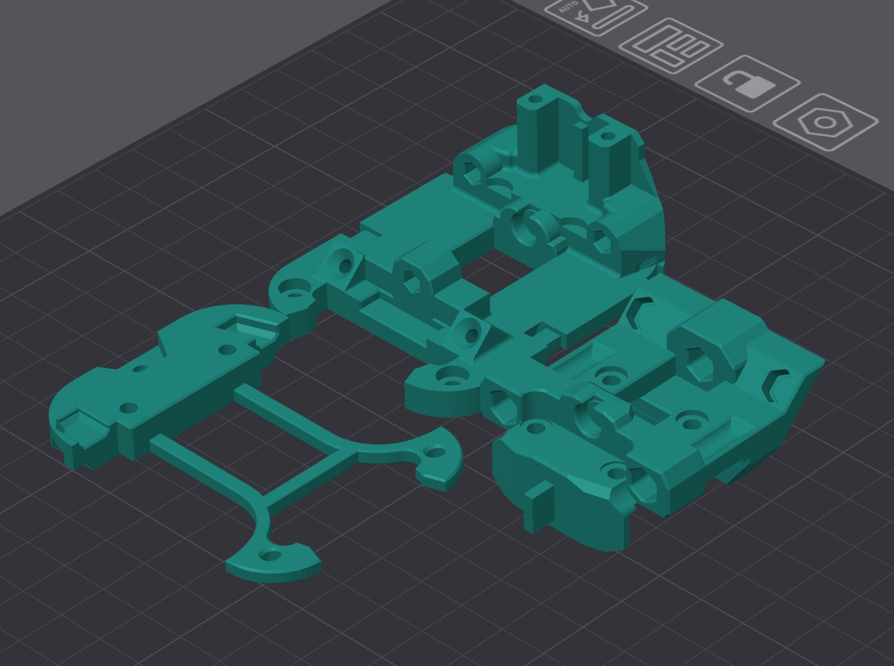
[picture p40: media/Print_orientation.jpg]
Print Orientation


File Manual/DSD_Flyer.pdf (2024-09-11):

# DRAFTSHIFT DESIGN

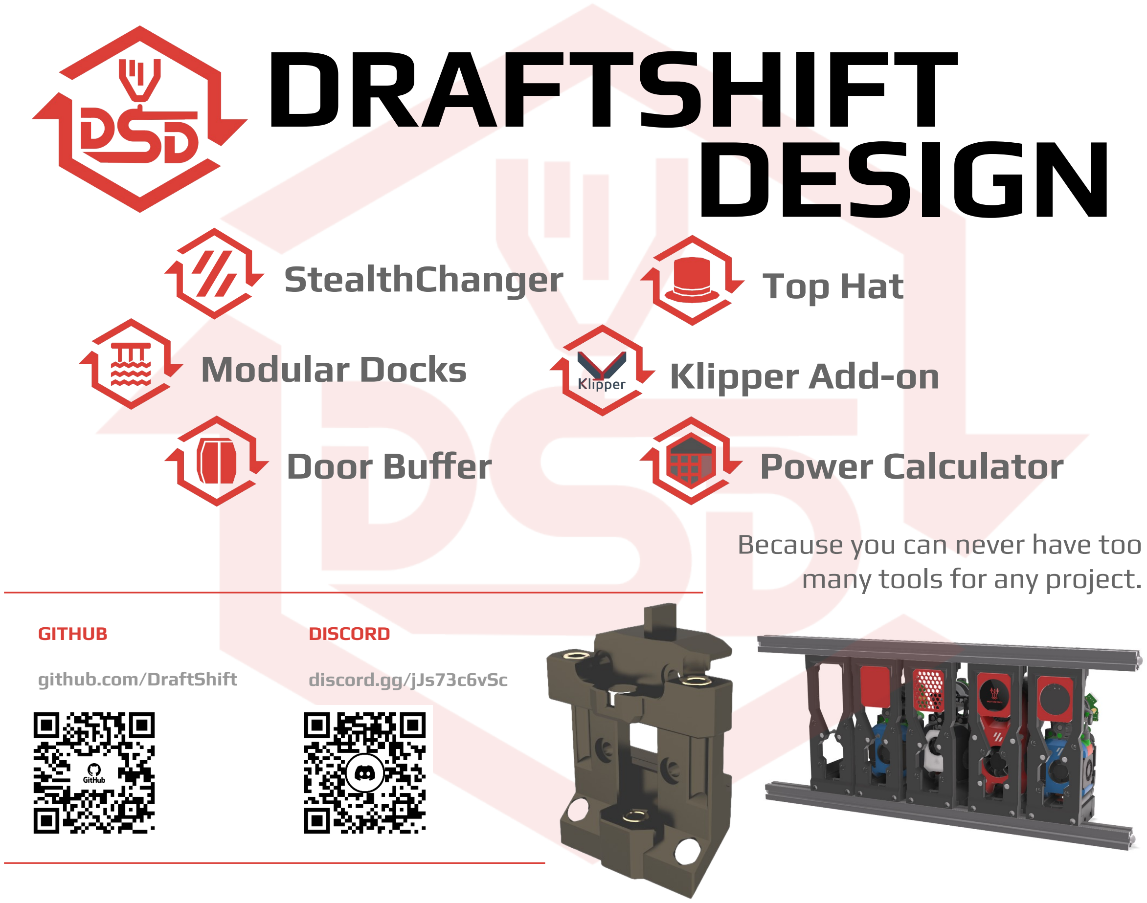
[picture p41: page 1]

GITHUB

github.com/DraftShift

DISCORD

discord.gg/jJs73c6vSc

Power Calculator

Modular Docks

Top Hat

Door Buffer

StealthChanger

Klipper Add-on

Because you can never have too many tools for any project.

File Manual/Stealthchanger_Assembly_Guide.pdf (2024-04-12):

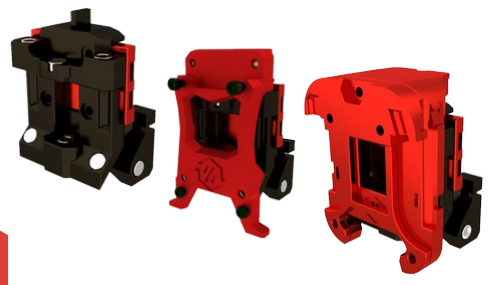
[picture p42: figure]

# STEALTHCHANGER V1 BUILD GUIDE

# Because you can never have too many tools

for any project.

# VERSION 2024-04-12

# DRAFTSHIFT DESIGN

PREFACE | GITHUB.COM/DRAFTSHIFT/STEALTHCHANGER

Before you begin on your journey, a word of caution.

In the comfort of your own home you are about to assemble a robot. This machine can maim, burn, and electrocute you if you are not careful. Please do not become the first STEALTHCHANGER fatality. There is no special Reddit flair for that.

Please, read the entire manual before you start assembly. As you begin wrenching, please check our Discord channels for any tips and questions that may halt your progress.

Most of all, good luck!

THE DRAFTSHIFT DESIGN TEAM

2

## TABLE OF CONTENTS

Introduction | 04
Hardware | 07
Shuttle | 08
Stealthburner | 11
Dragonburner | 14
Attaching to Carriage | 17
End Stop Options | 21
Next Steps | 22

3

## GITHUB.COM/DRAFTSHIFT/STEALTHCHANGER

## INTRODUCTION

PART PRINTING GUIDELINES

The Voron Team has provided the following print guidelines for you to follow in order to have the best chance at success with your parts. The StealthChanger Team recommends to follow the same standards. There are often questions about substituting materials or changing printing standards, but we recommend you follow these:

3D PRINTING PROCESS
Fused Deposition Modelling (FDM)

MATERIAL
ABS

LAYER HEIGHT
Recommended: 0.2mm

EXTRUSION WIDTH
Recommended: Forced 0.4mm

INFILL TYPE
Grid, Gyroid, Honeycomb, Triangle or Cubic

INFILL PERCENTAGE
Recommended: 40%

WALL COUNT
Recommended: 4

SOLID TOP/BOTTOM LAYERS
Recommended: 5

4

## INTRODUCTION

FILE NAMING

By this time you should have already downloaded our STL files from the StealthChanger GitHub. You might have noticed that we have used the Voron naming convention for the files. This is how to use them.

PRIMARY COLOUR

Example part_x4.stl

These files will have nothing at the start of the filename.

ACCENT COLOUR

Example [a]_part.stl

We have added “[a]” to the front of any STL file that is intended to be printed with accent colour.

QUANTITY REQUIRED

Example [a]_part_x4.stl

If any file ends with “_x#”, that is telling you the quantity of that part required to build the machine.

HOW TO GET HELP

If you need assistance with your build, we are here to help. Head on over to our Discord group and post your questions. This is our primary medium to help STEALTHCHANGER Users and we have a great community that can help you out if you get stuck.

### https://discord.gg/jJs73c6vSc

5

## INTRODUCTION

REPORTING ISSUES

Should you find an issue in the documentation or have a suggestion for an improvement please consider opening an issue on GitHub (https://github.com/DraftShift/Stealthchanger/issues). When raising an issue please include the relevant page numbers and a short description; annotated screenshots are also very welcome. We periodically update the manual based on the feedback we get.

THIS IS JUST A REFERENCE

This manual is designed to be a simple reference manual. Building a StealthChanger can be a complex endeavour and for that reason we recommend downloading the CAD files off our Github repository if there are sections you need clarification on. It can be sometimes be easier to follow along when you have the whole assembly in front of you.

### https://github.com/DraftShift/StealthChanger

6

## HARDWARE REFERENCE

BUTTON HEAD CAP SCREW (BHCS) Metric fastener with a domed shape head and hex drive. Most commonly found in locations where M5 fasteners are used. ISO 7380-1 | SOCKET HEAD CAP SCREW (SHCS) Metric fastener with a cylindrical head and hex drive. The most common fastener used on the Voron. ISO 4762
FLAT HEAD COUNTERSUNK SCREW (FHCS) Metric fastener with a cone shaped head and a flat top. ISO 10642 | HEAT SET INSERT Heat inserts with a soldering tip so that they melt the plastic when installed. As the plastic cools, it solidifies around the knurls and ridges on the insert for excellent resistance to both torque and pull-out.
BUSHING/SLEEVE BEARING Brass cindered are the most common. They should be self lubricating and metal construction. | ROUNDED DOWEL PIN Steel rounded dowel pin, These are commonly using in furniture construction. Female threaded versions are optional.

MAGNET Metric round button neodymium magnet used on the Voron. N52 is highly recommended.

7

## SHUTTLE

INSERT BUSHINGS

Inspect the bushing hex holes, make sure they are 6mm between walls of the hex. Make sure the hex is well formed. This is an important step as it could cause misalignment later on.

Apply a small amount of epoxy or glue to the inside of the hex (be sparing as you do not want any inside the the bushing).

Push the bushing into the hex and let sit until the epoxy or glue dries.

NOTE: Wipe any excess away and make sure none goes inside the bushing.

NOTE: you may be able to friction fit the bushings to test before your affix them permanently.

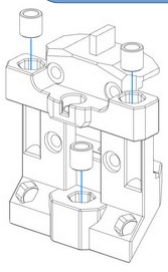
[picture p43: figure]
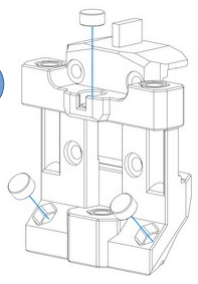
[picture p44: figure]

INSERT MAGNETS

Apply a small amount of epoxy or glue to the inside of the opening.

Push the magnet into the opening and let sit until the epoxy or glue dries.

NOTE: you may be able to fiction fit the magnets to test before your affix them permanently.

## 4 ID x 6 OD x 6mm Bushing

## 6x3mm Magnet

8

## SHUTTLE

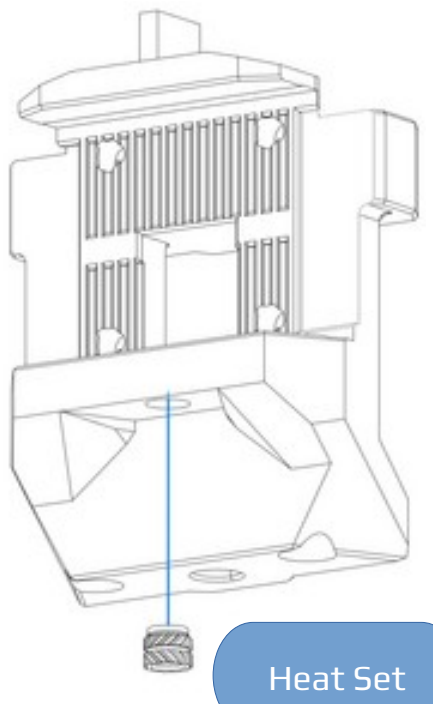
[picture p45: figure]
Heat Set

OPTIONAL INSERT HEAT SET

Optionally insert the end stop heat set. Only required if you are not using sensorless.

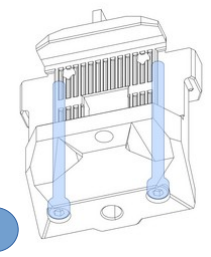
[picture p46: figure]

OPTIONAL SPINE SCREWS

Optionally screws can be inserted to add rigidity to the shuttle if your not happy with it’s stiffness

## M3x40mm SHCS

9

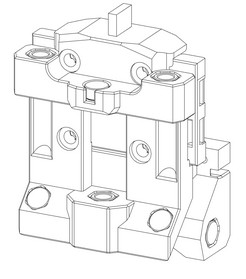
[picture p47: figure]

FINISHED SHUTTLE

This is the finished shuttle with options shuttle keeper (later in this manual) and the optional Hall Effect end stop attachment (later in this manual).

## SHUTTLE

10

## STEALTHBURNER

INSERT HEAT SETS

Start by setting the heat sets.

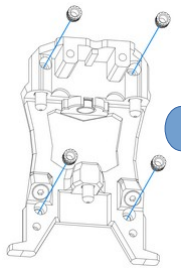
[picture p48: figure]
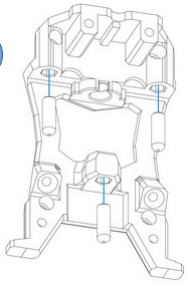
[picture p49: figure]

INSERT DOWEL PINS

Inspect the pin hex holes, make sure they are 4mm between walls of the hex. Make sure the hex is well formed. This is an important step as it could cause misalignment later on.

Apply a small amount of epoxy or glue to the inside of the hex.

Push the pins into the hex and let sit until the epoxy or glue dries.

NOTE: You may be able to friction fit the pins to test before your affix them permanently.

NOTE: You should test fit the pins onto the plate and the plate with the pins on the shuttle before making them permanent.

NOTE: Make sure to wipe away any excess so your can have a full sit into the bushings.

## Heat Set

## 4 OD x 12mm Pins

11

## STEALTHBURNER

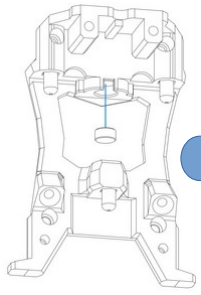
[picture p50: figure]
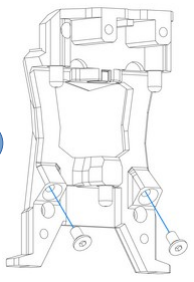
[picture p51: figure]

PRELOAD SCREWS

Insert the preload screws all the way, do not over tighten, we will set these later in this document (See Next Step). These just thread into the printed part without a heat set.

NOTE: These screws need to be magnetic like used in Voron Tap.

INSERT MAGNETS

Apply a small amount of epoxy or glue to the inside of the opening.

Push the magnet into the opening and let sit until the epoxy or glue dries.

NOTE: you should be able to fiction fit the magnets to test before you affix them permanently.

## 6x3mm Magnet

## M3x8mm FHCS

12

## STEALTHBURNER

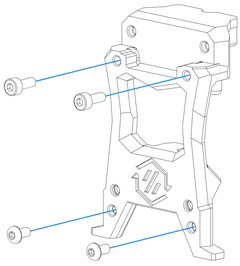
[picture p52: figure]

PREPARE FOR STEALTHBURNER

Install the screws to click on the stealthburner bottom piece. See stealthburner guild for screw sizes.

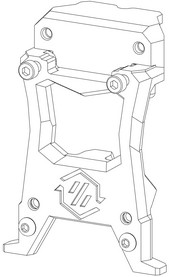
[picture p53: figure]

FINISHED TOOL PLATE

This is the finished stealthburner tool plate now continue with the official stealthburner guide from the Voron team.

NOTE: you may need to use longer screws when attaching the CW2.

13

## DRAGONBURNER

INSERT HEAT SETS

Start by setting the heat sets.

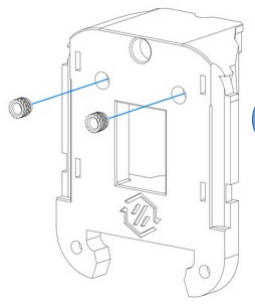
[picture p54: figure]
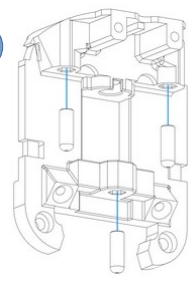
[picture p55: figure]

INSERT DOWEL PINS

Inspect the pin hex holes, make sure they are 4mm between walls of the hex. Make sure the hex is well formed. This is an important step as it could cause misalignment later on.

Apply a small amount of epoxy or glue to the inside of the hex.

Push the pins into the hex and let sit until the epoxy or glue dries.

NOTE: You may be able to friction fit the pins to test before your affix them permanently.

NOTE: You should test fit the pins onto the plate and the plate with the pins on the shuttle before making them permanent.

NOTE: Make sure to wipe away any excess so your can have a full sit into the bushings.

## HeatSet

## 4 OD x 12mm Pins

14

## DRAGONBURNER

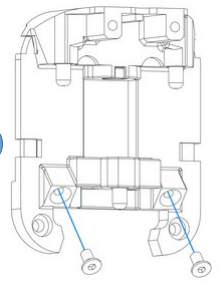
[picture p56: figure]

PRELOAD SCREWS

Insert the preload screws all the way, do not over tighten, we will set these later in this document (See Next Step). These just thread into the printed part without a heat set.

NOTE: These screws need to be magnetic like use in Voron Tap.

INSERT MAGNETS

Apply a small amount of epoxy or glue to the inside of the opening.

Push the magnet into the opening and let sit until the epoxy or glue dries.

NOTE: you should be able to fiction fit the magnets to test before you affix them permanently.

## 6x3mm Magnet

## M3x8mm FHCS

15

## DRAGONBURNER

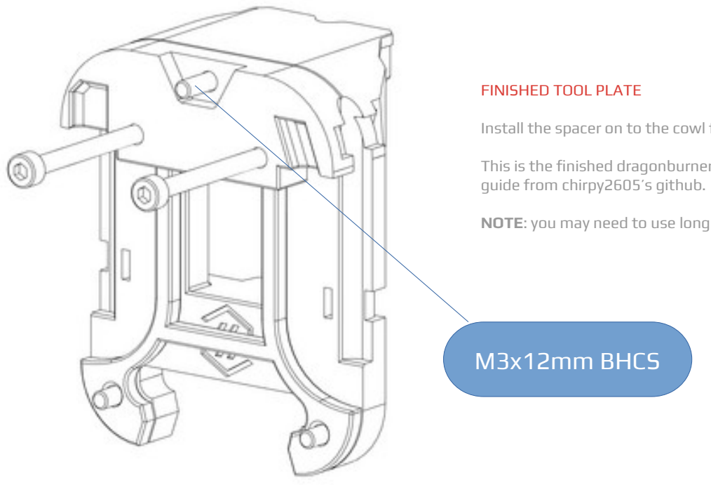
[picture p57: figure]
FINISHED TOOL PLATE; guide from chirpy2605’s github.; M3x12mm BHCS

Install the spacer on to the cowl first, then using the front cowl bolt add the backplate.

This is the finished dragonburner tool plate now continue with the official dragonburner

NOTE: you may need to use longer screws when attaching the cowl.

16

## ATTACHING TO CARRIAGE

SHUTTLE KEEPER

This is the easiest option, you loop the belts through the keeper, and then install it between the carriage and the shuttle using BHCS screws. You need longer screws to be able to go through both. Make sure you tighten the shuttle well.

Now adjust your belts as per standard Voron adjustments using the idlers.

OPTIONS

There are 2 options when it comes to attaching the belts and installing the shuttle to the X carriage.

1. You can use the shuttle keeper, this is the easiest way to install it the belts and allows for you to remove the shuttle without having to remove the belts. The down side is that you lose about 5mm of Y travel.
2. You can use the belt Helper tool to push the belts behind the shuttle and tighten the carriage screws which will pinch the belts between the carriage and the shuttle.

We will go though both options in this section but you only need to choose one.

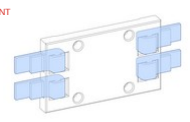
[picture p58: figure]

FRONT

BACK

INSTALL ORIENTATION

17

## ATTACHING TO CARRIAGE

BELT HELPER

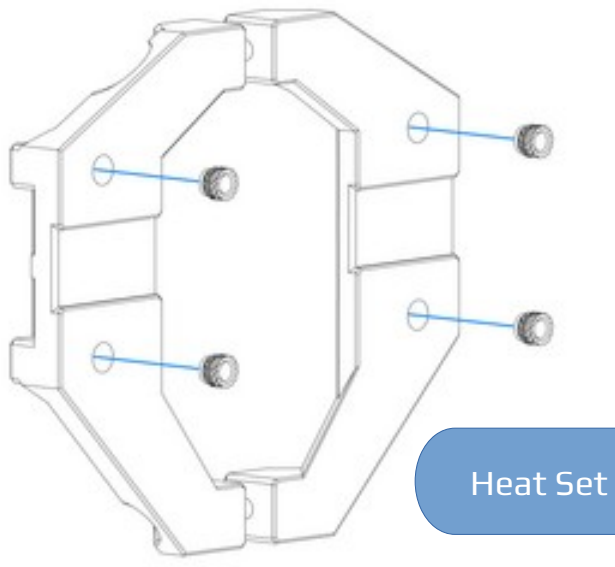
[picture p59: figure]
Heat Set

INSERT HEAT SETS

Start by setting the heat sets.

## Heat Set

18

## ATTACHING TO CARRIAGE

INSERT SCREWS

Add the belt clamps, make sure to match the icons with the right sides.

Install the belt clamp screws loosely.

Install the clamping screws loosely.

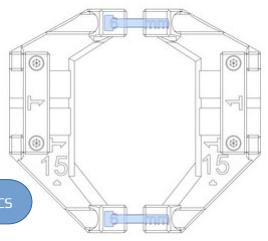
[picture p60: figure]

## M3x20mm SHCS

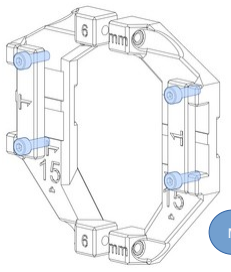
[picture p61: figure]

## M3x10mm SHCS

19

## ATTACHING TO CARRIAGE

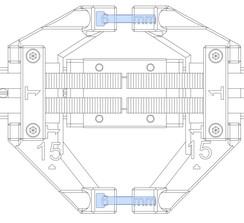
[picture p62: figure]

INSERT THE BELTS

Insert the belts, Making sure that there are 15 belt ridges on the inside of the helper. Makes sure you tighten the belt clamps well so the belt doesn’t slip.

NOTE: there is no need to pull hard the belts, just make sure there is no slack, if you pull too hard at this point you will over tighten the belts a could damage other components.

Next start to tighten the top and bottom screws, make sure your try to do this evenly until you measure 6mm between left and right side at the top and bottom evenly.

INSTALL THE SHUTTLE

NOTE: you must wait until after the shuttle is installed before adding any end stops if you are using one.

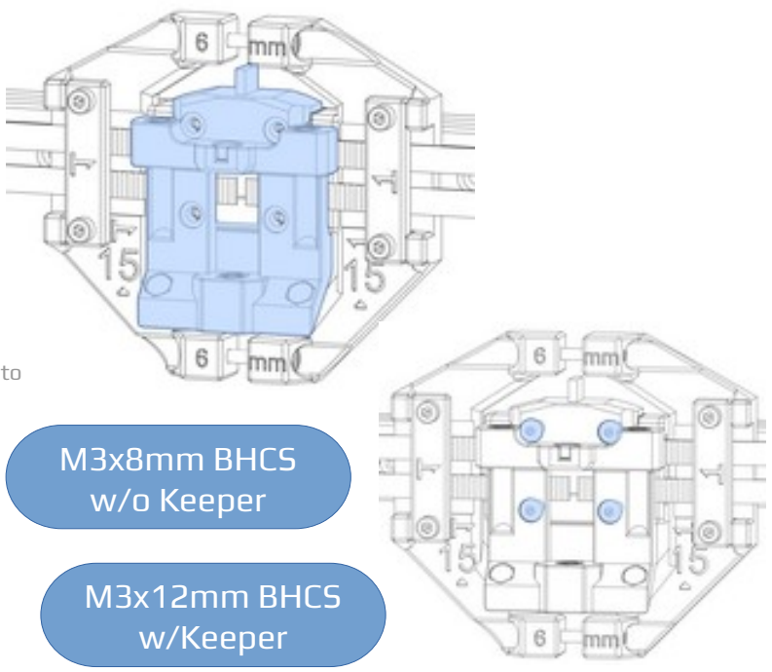
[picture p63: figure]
M3x8mm BHCS w/o Keeper; M3x12mm BHCS w/Keeper

The belt ends should be nearly touching, at this point install the shuttle and tighten it to the carriage using BHCS screws as per Voron Manual. Make sure things are nice and tight before you start to replace the helper.

Once you are ready, slowly undo the top and bottom screws evenly. Once there is enough slack you may remove the clamps on the belts and remove the helper.

Now adjust your belts as per standard Voron adjustments using the idlers.

20

## END STOP OPTIONS

OPTIONS

There are a few options when it comes to end stops. Hall Effect is a Voron stands as well as end stop switches. The team doesn’t provide the switch side, but we do have attachment points for and suppose to most common activation arms.

NOTE: more options may be available and are welcome.

HALL EFFECT
INSERT MAGNETS

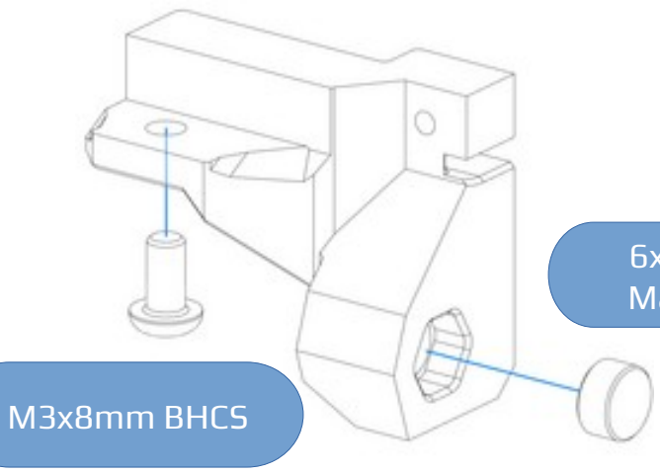
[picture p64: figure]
M3x8mm BHCS

Apply a small amount of epoxy or glue to the inside of the opening.

Push the magnet into the opening and let sit until the epoxy or glue dries.

NOTE: you should be able to fiction fit the magnets to test before you affix them permanently.

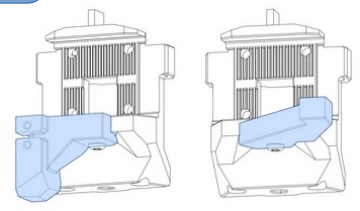
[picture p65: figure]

INSTALL THE END STOP ACTIVATION ARM

Simply screw it into the back side of the shuttle.

NOTE: Hall Effect and X Switch pictured.

## 6x3mm Magnet

21

## NEXT STEPS

ASSEMBLY COMPLETED!

The last step is to set preload. This should be done on each tool separately as it’s meant to help counter inconsistencies/variances in the parts.

Preload is created with the 2 countersunk screws in the tool plate. These 2 screws need to be magnetic and will make contact with the magnets in the shuttle. This adds 2 more wider points of contact at the base while also pre loading the sleeves/bearings. To adjust them screw them all the way in, then slowly unscrew them 1/4 turn at a time (keeping each side even) until the tool no longer engages its self right away. Once you reach a point where this happens, screw them back in 1/4 turn. Each tool needs to be adjusted separately as printing irregularities can happen and this will allow you to compensate for it. You may want to test and readjust these from time to time.

### https://github.com/DraftShift/Stealthchanger/wiki/Installation

22

NEXT STEP: SETUP & CALIBRATION

This manual is designed to be a reference manual for the build process of a StealthChanger.

The software setup and other initial setup steps with your new toolchanger can also be found on our github page. We recommend starting there.

Enjoy your toolchanger.

23

GITHUB

github.com/DraftShift

DISCORD

discord.gg/jJs73c6vSc

# DRAFTSHIFT DESIGN

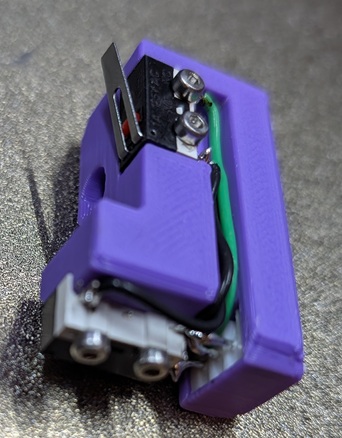
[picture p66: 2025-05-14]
UserMods/N3MI-DG/Endstop_Mounts/images/solder2.jpg

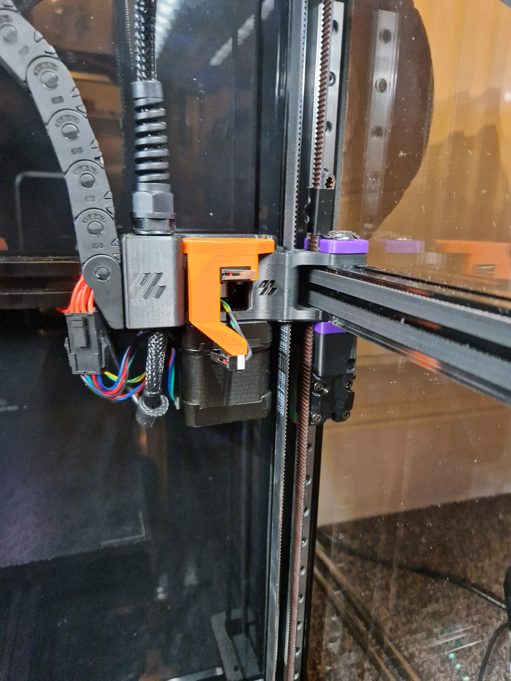
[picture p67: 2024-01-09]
UserMods/VIN-y/Endstops/Images/Endstop_assembly.jpg

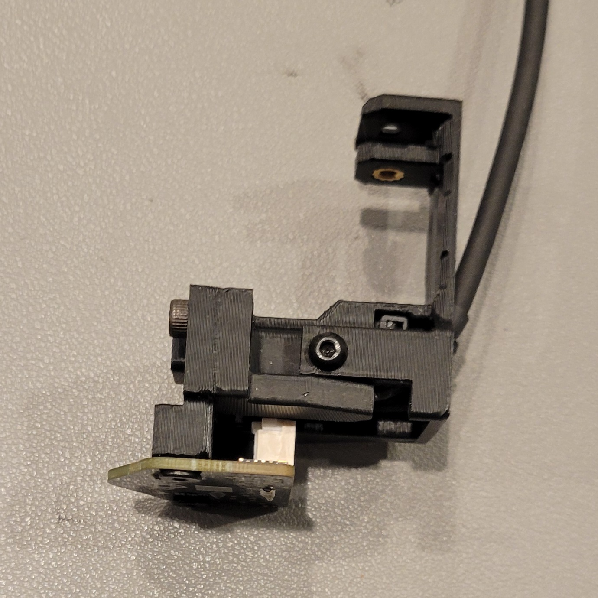
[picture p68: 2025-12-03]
UserMods/cekim-git/CNCShuttleMount/v1.2/media/brace_installed.jpg

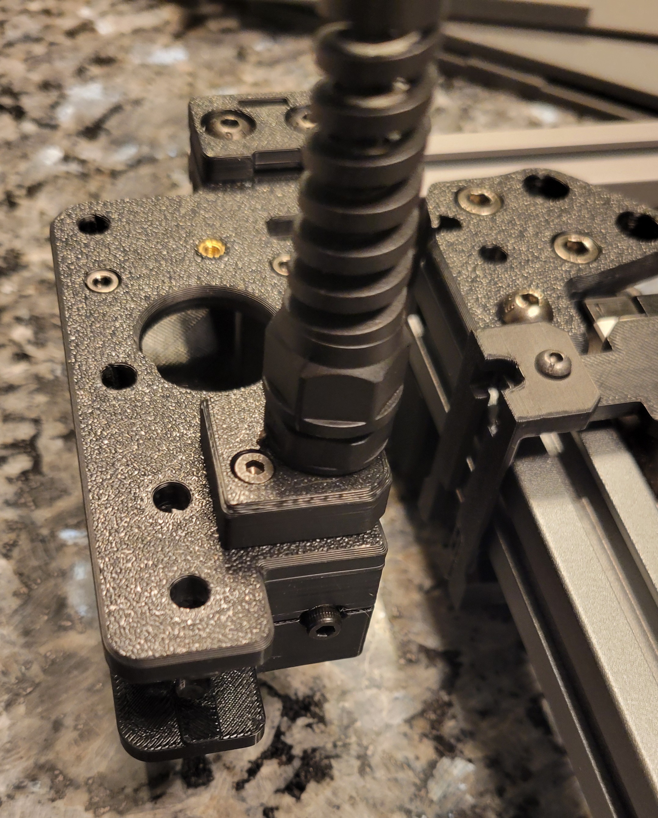
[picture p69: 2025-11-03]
UserMods/cekim-git/LowProfileGantryPG7Mount/v1.0/media/printed_gantry_mount.jpg

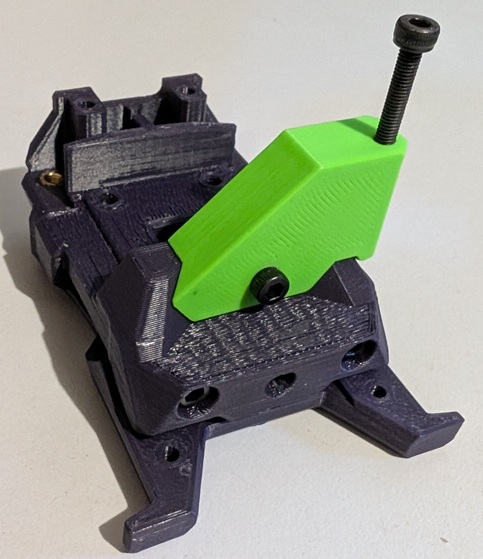
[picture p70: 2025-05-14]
UserMods/N3MI-DG/Endstop_Mounts/images/printed.jpg

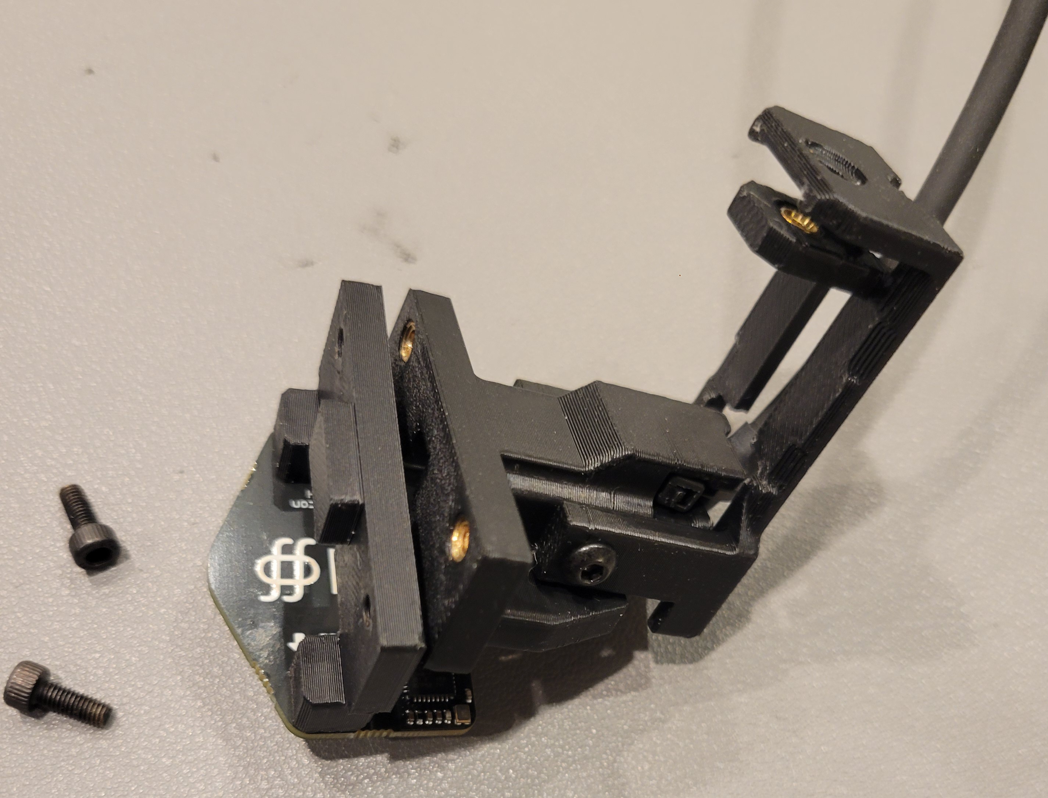
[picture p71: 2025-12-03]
UserMods/cekim-git/CNCShuttleMount/v1.2/media/temp_brace_uninstall.jpg

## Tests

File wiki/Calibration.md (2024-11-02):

1. [Z Offset](#z-offset)
2. [GCODE Z Offset](#gcode-z-offset)
3. [Dock Parking](#dock-parking)
4. [X/Y Offset](#xy-offset)
5. [Manual Paper Test](#manual-paper-test)

**Before you start calibrating you must "break-in" each tool probe.  Heat soak your machine and run a couple `PROBE_ACCURACY SAMPLES=100` per tool.**

## Z Offset

**NOTE:** Tn is the tool on the shuttle, ie T0

1. Put a tool on the shuttle and run `INITIALIZE_TOOLCHANGER`
2. Run `G28`
3. Run `QUAD_GANTRY_LEVEL`
4. Run `G28`
5. Do a [Manual Paper Test](#manual-paper-test) as normal like a single toolhead head printer and adjust the Z
5. Copy the offset and save this to `z_offset` in `[tool_probe Tn]` of the tool conf file
6. Repeat from `step 1` for all tools (`step 2` and `step 3` are optional after first tool)
7. Run `FIRMWARE_RESTART`

## GCODE Z Offset

**NOTE:** Tn is the tool on the shuttle, ie T1

**NOTE:** only home or probe with T0 during this calibration

**NOTE:** `gcode_z_offset` on Tool 0 is always 0.

1. Set [z_offset](#z-offset) for all tools first
2. Make sure T0 is on the shuttle and run `INITIALIZE_TOOLCHANGER`
3. Run `G28`
4. `QUAD_GANTRY_LEVEL` 
5. Run `G28`
6. Run `G1 Z10 F600`
7. Manually remove current tool and place the next tool in its place on the shuttle
8. Do a [Manual Paper Test](#manual-paper-test) as normal like a single toolhead head printer and adjust the Z
9. Once done run `M114` and copy the Z value to `gcode_z_offset` in `[tool Tn]` of the tool conf file
10. Repeat from `step 6` for all tools
11. Run `FIRMWARE_RESTART`

## Dock Parking

**NOTE:** Set the `params_close_y` to your highest `params_park_y` + 30, and set `params_safe_y` to `params_close_y` + the thickness of your thickest tool + 10 in the `toolchanger.cfg` and **remove them from the tool config files**

**NOTE:** For `params_safe_y` you could also just make sure when you have a tool on the shuttle you can move freely behind the dock and not hit any other docked tools and note that `y` position.

1. Put a tool on the shuttle and run `INITIALIZE_TOOLCHANGER`
2. Run `G28` and `QUAD_GANTRY_LEVEL` 
3. Remove the tool from the shuttle and place it in the dock
4. Move the gantry as if to pick up the tool, as soon as the light on the optotap pcb changes
5. Raise Z by 1
6. Run `M114` and record the values to `params_park_x`, `params_park_y` and `params_park_z` in `[Tool Tn]` of the tool conf file
7. Run `G28`
8. Run `SET_TOOL_PARAMETER PARAMETER='params_path_speed' VALUE=300`
9. Run `TEST_TOOL_DOCKING RESTORE_AXIS=XYZ`
10. Run `RESET_TOOL_PARAMETER PARAMETER='params_path_speed'`
11. Repeat this for all tools
12. Run `FIRMWARE_RESTART`

### Docking/Undocking

The Moving using config parameters is as such:

| Current tool | No tool | Next tool |
|---|---|---|
|`safe_y`, `park_x` -> `park_z` -> `close_y` -> `path` | `close_y` -> `park_x` | `path` -> `safe_y` -> `t_command_restore_axis` |

## X/Y Offset

**NOTE:** `gcode_x_offset` and `gcode_y_offset` on T0 are always 0

### [Sexball Probe](Bill-of-Materials#sexball-probe) or [NozzleAlign](https://github.com/viesturz/NozzleAlign)

Follow the guide at [NozzleAlign](https://github.com/viesturz/NozzleAlign)

### [Print STL](https://www.printables.com/model/201707-x-y-and-z-calibration-tool-for-idex-dual-extruder-)

Follow the guide at [Print STL](https://www.printables.com/model/201707-x-y-and-z-calibration-tool-for-idex-dual-extruder-)

### Camera or [kTAMV](https://github.com/TypQxQ/kTAMV)

Follow the guide at [kTAMV](https://github.com/TypQxQ/kTAMV)

### [Nudge](https://github.com/zruncho3d/nudge)

Follow the guide at [Nudge](https://github.com/zruncho3d/nudge)

## Manual Paper Test

The primary bed calibration mechanism is the "paper test". It involves placing a regular piece of "copy machine paper" between the printer's bed and nozzle, and then commanding the nozzle to different Z heights until one feels a small amount of friction when pushing the paper back and forth.

It is important to understand the "paper test" even if one has an "automatic Z probe". The probe itself often needs to be calibrated to get good results. That probe calibration is done using this "paper test".

In order to perform the paper test, cut a small rectangular piece of paper using a pair of scissors (eg, 5x3 cm). The paper generally has a thickness of around 100 microns (0.100mm). (The exact thickness of the paper isn't crucial.)

The first step of the paper test is to inspect the printer's nozzle and bed. Make sure there is no plastic (or other debris) on the nozzle or bed.

**Inspect the nozzle and bed to ensure no plastic is present!**

If one always prints on a particular tape or printing surface then one may perform the paper test with that tape/surface in place. However, note that tape itself has a thickness and different tapes (or any other printing surface) will impact Z measurements. Be sure to rerun the paper test to measure each type of surface that is in use.

If there is plastic on the nozzle then heat up the extruder and use a metal tweezers to remove that plastic. Wait for the extruder to fully cool to room temperature before continuing with the paper test. While the nozzle is cooling, use the metal tweezers to remove any plastic that may ooze out.

**Always perform the paper test when both nozzle and bed are at room temperature!**

When the nozzle is heated, its position (relative to the bed) changes due to thermal expansion. This thermal expansion is typically around a 100 microns, which is about the same thickness as a typical piece of printer paper. The exact amount of thermal expansion isn't crucial, just as the exact thickness of the paper isn't crucial. Start with the assumption that the two are equal (see below for a method of determining the difference between the two distances).

It may seem odd to calibrate the distance at room temperature when the goal is to have a consistent distance when heated. However, if one calibrates when the nozzle is heated, it tends to impart small amounts of molten plastic on to the paper, which changes the amount of friction felt. That makes it harder to get a good calibration. Calibrating while the bed/nozzle is hot also greatly increases the risk of burning oneself. The amount of thermal expansion is stable, so it is easily accounted for later in the calibration process.

**Use manual controls to move the tool**

Using the webUI (Mainsail, Fluidd, Octoprint) or the LCD Controls, move the tool down and stop just before the bed.  Place the paper between the nozzle and bed. It can be useful to fold a corner of the paper so that it is easier to grab. (Try not to push down on the bed when moving the paper back and forth.) Continue to jog the tool down 0.1 at a time. After the nozzle stops moving, push the paper back and forth to check if the nozzle is in contact with the paper and to feel the amount of friction.

If too much friction is found then jog up be smaller increments.

Once you are happy with the results note the Z position (you may also use `M114` to get the location).

*Taken from Klipper [paper test](https://www.klipper3d.org/Bed_Level.html#the-paper-test)*

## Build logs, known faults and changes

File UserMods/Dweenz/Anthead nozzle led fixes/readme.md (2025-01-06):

A simple mod of N3MI's nozzle LED for ANTHEAD SF. The Mainbodies are labeled VORONLOGO. UHF means ultra high flow, HF means high flow. Then the extruder type sherpa mini, or orbiter. The LED's need to be split to object in slicer and oriented correctly.

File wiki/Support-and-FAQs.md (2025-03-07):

1. [Methods](#methods)
2. [FAQs](#faqs)
3. [Build Guide](#build-guide)
4. [Macros](#macros)

## Methods



## FAQs

### Check your print quality
After printing the parts make sure that the hex holes look to be proper hexes and that they are very uniform.  If they are misshapen chances are you need to reprint as you will have alignment issues.  It doesn't take much to be out by a lot.  Try printing at a slower speed if you have issues.

### What probes can be use with SC?
TAP is baked in to each tool as part of SC. As of right now no other probes are compatible with the printed parts or with klipper since only open probe can exist at a time.  Thus only TAP can be used.

### How many tool will fit on my printer?
Calculating available size for tools (number of tools you can fit)
   - Dragon Burners/Yavoth require 60mm per tool (I recommend 5mm between for extruder handles)
   - Blackbird, Stealth Burners and XOL require 76mm per tool
   - The gantry required about 20mm per side to be able to pass the tools.  To know how many tools you can fit it's simple math, measure that top bar -40mm to gantry and then divide the remainder by the size of your toolhead.

### Tophat: Is it required?
If you only want to print PLA or filaments that dont require an enclosure there is no need just like on the prusa XL. With ABS ASA ect you will need to enclose it.

**How tall should it be?** for a 350 build we found 250mm, 300 build 225mm and 250 build 200mm additional z height works out well though might need to be higher depending on where you pass through umbilicals. It needs only be enough so that the cables can have a nice arch from back to front so not to collide with others and tangle, while being long enough to reach the farthest corner on the buildplate at layer 1.

### Adjust preload
Preload is created with the 2 countersunk screws in the tool plate.  These 2 screws need to be magnetic and will make contact with the magnets in the shuttle.  This adds 2 more wider points of contact at the base while also pre loading the sleeves/bearings.  To adjust them screw them all the way in, then slowly unscrew them 1/4 turn at a time (keeping each side even) until the tool no longer engages its self right away.  Once you reach a point where this happens, screw them back in 1/4 turn.  Each tool needs to be adjusted separately as printing irregularities can happen and this will allow you to compensate for it.  You may want to test and readjust these from time to time.

### QGL won't finish
If you run homing on Z or QGL and you are getting lots of restarts or excessive runs.  Make sure you are using **N52** magnets, and check that your umbilicals are properly support and the right length.  If these 3 things aren't checked it will affect the tap precision.

### Gantry won't go low enough (Voron-V2)
Some tools are shorter than others and with some of the shorter tools the z-rail carriages reach the end of their travel before the nozzle can reach the bed, this can be a problem for probing, QGL and printing.

There's a few options to solve this:
- remove or modify the Z-belt-covers
- replace stock z-joints with [Rigid Z joint](https://www.printables.com/model/996313-voron-v24-rigid-fixed-z-joint) or [low profile z-joints](https://mods.vorondesign.com/details/1hy4XR47A0UJYaDhizaFg)
- Use taller bed spacers

### Which toolhead/extruder is recommended?
A lot of people are asking which toolhead/extruder is recommended. The answer is whatever you want. The changer and tools are completely separate. That being said, using something that is officially supported is going to be the easiest.

### CAN setup
You are definitely going to want to use CAN to connect your toolheads. Its only 4 wires and much lighter. You don't need anything fancy to split out the signal. Simple WAGO connectors work just fine. Of course, there are options for boards that will split the signal as well if you want something that looks a little more professional. Run wires up to the umbilical from your controller and power supply, then use WAGO's there to split the signal. See the guide [here](Configuration#canbus) for a lot more CAN information.
   
### Make sure you have a good PID
If you try to change tools during a print (or when the hotends are active) and it drops off one tool, then waits behind another tool and does nothing, the issue is that its probably waiting for the tool temp to stabilize. Make sure you run a PID tune for each tool and place the info in the corresponding tool config.

### How to calculate build loss
On a stock Voron you will loose some build volume, that build volume loss is in the Y and Z areas on the front of the build plate.  To determine this you ened to know where you docks are and the dementions of your tool.  We have included an image to help you visualize and calculate the loss under and behind the docks.

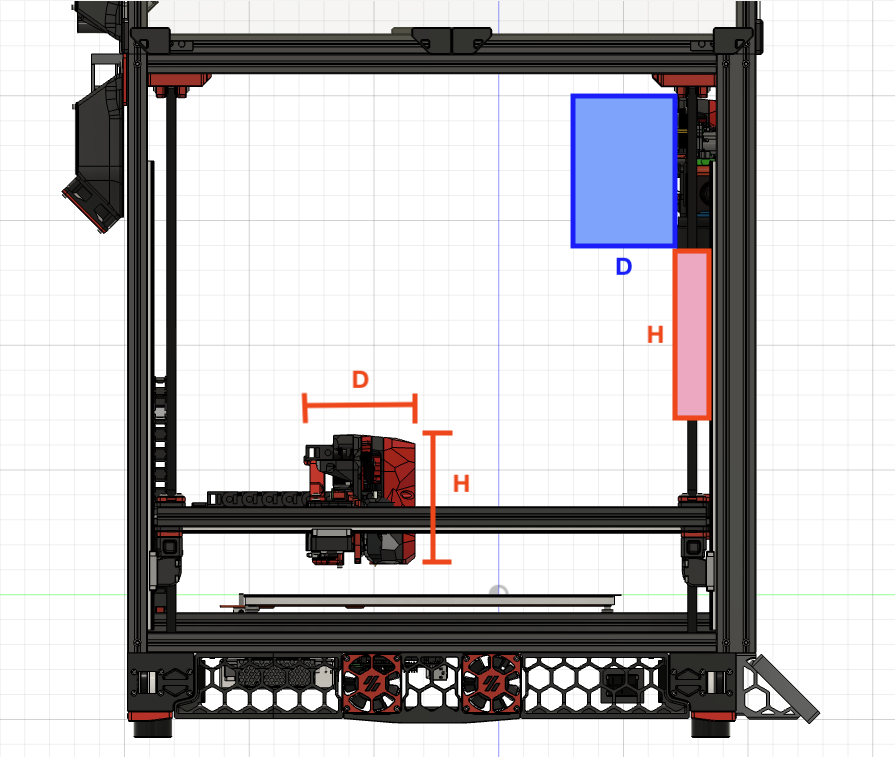
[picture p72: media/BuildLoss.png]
Build loss


## Build Guide
**Built on stream by [ZombieHedgehog](https://www.twitch.tv/zombiehedgehog)**

| Episode | |
|--- |--- |
| 1 | https://youtu.be/YK2Zk2K584Y |
| 2 | https://youtu.be/yOGEAGLlvZc |
| 3 | https://youtu.be/W_r2b8U1J6k |
| 4 | https://youtu.be/cCbIjArKL4M |

## Macros

| Command | Description |
|--- |--- |
| Tool_Align_Start | This macro will put the toolhead 100mm away from where you set the docking position. |
| Tool_Align_Test | This macro will test the docking/undocking procedure. Start it from the docking position (start a few mm up on z, as the first movement is moving straight back on Y). |
| Tool_Align_Done | This macro will move the toolhead back away from the dock. |

* [Youtube Video](https://www.youtube.com/watch?v=mOSi8zTpu_Q) link showing each one

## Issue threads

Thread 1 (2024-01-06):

Holes too loose

viesturz, 2024-01-06:
Hey, I'm printing with quite spot-on dimensions, external perimenters first and the holes come out very loose.
The pins literally fall out and the bushings hold with minimal force.
The magnet holes are also quite oversized.

Also if you can update the instructions if they should be glued in place (recommended glue) or just press fitted.

viesturz, 2024-01-09:
Nope, just straight send to print.
I'm tuning my flow based on top layer, typically resulting in 0.94 for ASA. And printing with external perimeters first which gives pretty spot on to slightly undersized external dimensions.

My guess would be that external perimeters last should add about 0.1-0.2mm to each wall and would mostly resolve this.

Some pics for reference.

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

TheSin-, 2024-01-09:
for ref I always print perim first, not for or against but this might be way I could never get lit working for me properly.

TheSin-, 2024-02-08:
I've tuned my printer and I'm now seeing the same issues.

I'm working on figuring out the best approach since we can't really have users drilling/reaming parts cause there is no direct access.

TheSin-, 2024-03-05:
This is fixed just not released yet.

Closed 2024-03-14.

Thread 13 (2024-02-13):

Dragon burner spacer and backplate holes don't match

McPrince96, 2024-02-13:
The bottom holes of the dragonburner spacer and backplate don't match the dragonburner cowl found in tapchanger.
Could be that i'm doing something wrong but i don't think so.

Cowl i printed:
https://github.com/viesturz/tapchanger/blob/main/Tapchanger/STL/Toolheads/DragonBurner/Cowling.stl

TheSin-, 2024-02-13:
the issues isn't here, the one in the TapChanger repo is modified, you do not support the modified cowls, we only support the upstream cowls.

There is a merged version in one of the usermods, https://github.com/Hellsparks/StealthChanger/blob/main/UserMods/OstroMa/DB_Cowl_v8_with_TapChanger_Dock_Hooks.stl

Use that but it's a user mod and is not supported by the Stealthchanger team, we recommend using the original upstream cowl.

Closed 2024-02-13.

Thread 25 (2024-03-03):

Stealthburner Heat Sets

24Tigger24, 2024-03-03:
The Stealthburner's heat sets are located on a radius (see left side in the picture), which makes it difficult to get them into the correct position when inserting them.

My suggestion: a flat surface (see right side in the picture) and the heat sets sit under the surface or on the surface with longer screws used
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

TheSin-, 2024-03-03:
It has to be on that side due to the amount of pull force required by the CW2 assembly to get a good amount of stiffness.  We also wanted to use the same sized fasteners, which is why they are where they are,  might be able to make a silghtly larger opening to get to them.  But all our efforts are currently on v2 which does not have this issue as all anymore since the geometry on v2 has been completely redone.

TheSin-, 2024-03-05:
actually after re reading I like this, if we do an other v1 maintenance release we will add this.  @BT123D

Closed 2024-03-14.

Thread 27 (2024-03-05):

Write a "Before you start" wiki section

TheSin-, 2024-03-05:
We need to add a things to consider before you start

- Frame 2040 vs top mounted docks vs frame buffer, pros and cons
- things to consider for canbus
- things to consider for cable management
- answer the you should have tap on every tool
- etc...

TheSin-, 2024-03-05:
Maybe @BrewNinja can take this on?  Thoughts @BrewNinja ?

BrewNinja, 2024-03-05:
Sure can!

TheSin-, 2024-03-11:
Done in  https://github.com/Stealthchanger/Toolchanger/commit/eb3a9e1614d4aa0ad1b517eb68f17d1797640c4e

Closed 2024-03-11.

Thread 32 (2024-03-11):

[Suggestion] Split shuttle into two parts and glue them later

whyme12, 2024-03-11:
Hi,
When printing the shuttle I hade huge issues. Loosing the small details for the belt due to support and slicer doing weird stuff.

I ended up printing the part sliced in half and gluing it back together after printing.
- Its printed in ABS anyways and can easily be glued.
- Both sides have perfect details.
- The 4 Holes for the carriage can be used for Alignement

Only two downsides on the current model.
- The two holes on the bottom needed to be drilled after gluing
- there is no good plain to cut the part in half. So minor bridging/support is needed in the current model.

Not sure about the clearance, but if the IR sensor thingy and the plane behind the middle bushing could be moved 0.4mm lower then the belt feature, then there would be a perfect plane to split the part in half.

Here is an example of how I printed the part:
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

Martorias, 2024-03-11:
It shouldn't be a big problem to print with supports, mine came out great. Most likely you'll use the shuttle keeper to hold the belt anyways.
Either way, there's a v2 in the works that won't be needing supports.

whyme12, 2024-03-11:
don't know what went wrong, but had huge issue printing the part in the recommended way. Never hade such issues before.
Splitting the part made it fool proof in the end.

TheSin-, 2024-03-11:
splitting like this will cause LOTS of issues in the bushings. I would avoid this at all costs.  Once you are in a heated chamber I assume you will start to see other failures.

I'm closing this as I don't want to confuse others.

Having a properly tuned printing setup with tuned supports is a must.  We have builtin supports as a todo, so that's coming.

Closed 2024-03-11.

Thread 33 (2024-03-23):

(Dragonburner carrier) Fasteners for pins and discord

cekim-git, 2024-03-23:
Discord invite returns "invalid" for me.  I was hoping to discuss this mod.

Added M3 fasteners for the pins for rigidity/adjustment and ease of installation (no alignment + super-glue for pins
).  This began as a work-around to make straight pins function while I waited for long-lead-time rounded pins, but I've kept it with my rounded pin for all the above.

Mods:
1. Added through and recess holes for M3 fasteners (M3x8SHCS for the top pins, M3x4BHCS for the bottom)
2. Removed filleting in the bottom of the pin-hole (likely not needed - part of my experimentation to get straight pins and SS bushings I had on hand to work that I abandoned when rounded pins and brass bushings arrived and work much better).

Fusion360 and .step file

[StealthChanger_Dragonburner_Fastener_cekim.zip](https://github.com/Stealthchanger/Toolchanger/files/14733580/StealthChanger_Dragonburner_Fastener_cekim.zip)

BT123D, 2024-03-23:
Try this link

https://discord.gg/A5AUYTKU

TheSin-, 2024-03-23:
Since this can't be used for all backplates we will not include this, but this is addressed in v2 when it's ready, sine there is no PR and it looks like you used older version I'm just going to close this to not confuse other users.

Closed 2024-03-23.

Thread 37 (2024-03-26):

Build of material/BOM

julianvolden, 2024-03-26:
The BOM needs to be updated..
Does not tell you to order 3x12mm bhsc if planning to use the shuttlekeeper for the SB.

should also be updated with what printed parts that you need for the BOM option chosen.

my hotend is now dismantled, and obviously i need the belthelper to make it easier to install,and that stl was hidden under "usermod" and not STL.
so it was a 2step forward, 1step backward operstion for me 😅

TheSin-, 2024-03-26:
Sorry to here this, the belt helper is just a user tool to help it's not technically required, just like for stock Voron there are such tools as well but they aren't part of the BOM.

As for the bolts they are listed in the manual as it's an optional part.  We will see about adding them to the BOM

TheSin-, 2024-03-26:
Thank you I have updated the docs

Closed 2024-03-26.

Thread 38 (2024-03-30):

Old TAP pcb mounting offset not compatible with current shuttle offsets

kiwidave72, 2024-03-30:
I have both the new TAP PCB and old v5 PCB functionally they are fine.

Issue: that the old v5 PCB mounting holes make the PCB mount to low on the backplates (dragonburner, and possibly the others).
Results from the Issue: when docking the top of the TAP flag (if you can call it that) can catch on the PCB when moving into position.
When other tool heads are bring picked up. The Top belt of the XY gantry can catch on the PCB of the tool head with the PCB install.

Solution: Warning on manual that the old PCB's are not supported. and that the PCB must be flush with the backplate.
Change tool docking paths to move shuttle under the PCB when docking.

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

TheSin-, 2024-03-30:
Your board is upside down, turn it.

Also if you want to run it upside down just change you docking path.

v1 and v2 are fully compat I run both personally.

Closed 2024-03-30.

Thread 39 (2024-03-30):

Shuttle keeper is too loose

Ficik, 2024-03-30:
I needed to reprint the shuttle keeper and I noticed that I can't tention my belts, they're slipping thru the keeper.
I found out that commit 73256c1 `6mm Shuttle Keeper fix` offset shuttle keeper from mgn rail by 1mm, I agree that original 0.2mm was bit too tight for gt2, but 1.2mm can fit almost whole belt including teeth (1.38mm).

Since belt thickness without teeth is 0.63mm, spacing should be around that value (0.6mm).

Top view of the rail carrage with shuttle keeper. Blue is pre patch, black is post patch

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

TheSin-, 2024-03-30:
@BT123D

BT123D, 2024-03-30:
Can you show any evidence of this? I've just tested with mine and this is not the case.

The belt grooves are 0.6mm away from the metal face of the carriage to allow the 0.63mm of a gt2 belt, and they're 1mm away from the wipers. This is to account to variances in rails and because the belt should not be pressing on the wiper as this will cause issues

Ficik, 2024-03-31:
First I, need to apologize, I didn't have right cad model of mgn12h, so the image above is bit missleading it's mgn12c, length of the carriage is wrong. Here's new drawing:

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

As I was looking for proper dimensional drawing of mgn rail, I noticed that height of the bump of metal block body (or more precisely the depth of the valley between them) is not specified, neither is the height of green wipers and vary quite significantly between manufacturers. This probably explains why my belts slip and yours doesn't.

Anyway If you mean by wipers the whole green part then the only part that should clamp the belt in place is this highlighted one:

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

Which I'll argue that is rather small and bit too far from closest tooth (the one inside the hole) and that you actually are clamping the belt against the green wipers, mine are just bit lower than yours. After all almost all the teeth are above that part.

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

Step file of keeper on carriage: https://drive.google.com/file/d/1qZrFI_c3-GE3vv6t1esehQFsj6f-Y4Fj/view?usp=sharing

Step file of tweaked keeper: https://drive.google.com/file/d/1lZN_4F2ZRK3eo2AGeK-WC1YBED-E2koW/view?usp=sharing

BT123D, 2024-03-31:
Thank you for including the fixed step file for this. Sorry the current part didn't work for you but I'm happy that you could mod the keeper to work. Tomorrow I'll update to repo to suit your fix

TheSin-, 2024-04-01:
I have confirmed this issue for 6mm belts.

Closed 2024-05-25.

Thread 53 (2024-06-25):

Optional spine screws

AstronIsTaken, 2024-06-25:
Out of curiosity (since I'm printing new v1.1.1(?) shuttle) I tried to add spine screws to v1.1 shuttle and, unfortunately, shuttle cracked in between layers.  2nd screw hole I predrilled with M3 reamer almost all the way and screw went in flawlessly.

It might be hard to achieve perfect tolerances for such a long horizontally printed screw holes, so it might be good idea to add a note to guide to use reamer  before adding spine screws or increase screw holes diameter a bit.

TheSin-, 2024-06-27:
this is a good point thought oddly the first time it's been brought up, I'll look into it.

AstronIsTaken, 2024-06-27:
It might mean feature is not used at all you can just retire it. Or my tolerances are so bad or I had block stuck inside hole, so shuttle cracked

TheSin-, 2024-06-27:
Oh I know it's used by many as we talk about it, that being said shuttles aren't printed as much as tool plates so once it's working....

kiwidave72, 2024-06-29:
ive had a few issues, than i reprinted and reamer'ed out some plastic with a reamer until i could get the bushings in without craking. think this is more of a case by case thing as my printer isnt the best turned one in the world.

john-f-chamberlain, 2024-06-29:
Did you use fully threaded screws or are they only partially threaded? When added the spine screws to mine I noticed the ABS discoloring due to stress caused by the partially threaded section being slightly wider than the threaded section. I would imagine under certain circumstances this could add enough stress to cause the part to split.

TheSin-, 2024-06-29:
full thread

AstronIsTaken, 2024-06-29:
In my case I had partially threaded

On Sat, Jun 29, 2024, 11:00 Justin F. Hallett ***@***.***>
wrote:

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

TheSin-, 2024-06-29:
maybe we will change the document to say fully threaded then.  The issue is that you want it to be tight the entire length, I could open it half way for a shoulder but then the bottom wouldn't benefit from the spine as much.  And the bottom needs it the most.

Altirix, 2024-07-04:
yeah i actually had this happen to me with v1 because i used partially threadded screws on my first go. had way more of them. rummaged thru my misc unsorted screws and found fully threaded which were fine.

TheSin-, 2024-07-04:
Added notes to use fully threaded https://github.com/DraftShift/StealthChanger/commit/f7f19c9c4d7fe11cdcacf678c8a3aee60b2f2538

Closed 2024-07-04.

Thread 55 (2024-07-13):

Dragonburner_Spacer.step

leesafur, 2024-07-13:
Please add the Dragonburner Spacer step file to the cad folder. All spacers seem to be missing.

TheSin-, 2024-07-13:
It should be in the dragonburner backplate step already, I’ll check in the morning

TheSin-, 2024-07-13:
Confirmed the spacer is in the backpay file where it should be.

Closing ticket as it's invalid

leesafur, 2024-07-13:
This is where i'm looking CAD/Backplates/DragonBurner.step and its not in there. However I did find it in one of the forks that hasint been updated.

TheSin-, 2024-07-13:
I just opened that file directly from the repo it and it’s right there as it opens

leesafur, 2024-07-13:
This one has the spacer https://github.com/DraftShift/StealthChanger/blob/main/Legacy/V1/CAD/Backplates/StealthChanger_Dragonburner.step
This one is the newer version where the tap standoff is longer but theres no spacer. Will the V1 spacer work, it seems to fit fine. https://github.com/DraftShift/StealthChanger/blob/main/CAD/Backplates/DragonBurner.step

TheSin-, 2024-07-13:
Yes spacer wasn’t changed but it’s in the v1.1 step file

Closed 2024-07-13.

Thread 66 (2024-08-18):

Possible typo as well as wording issue in Stealthchanger_Assembly_Guide.pdf file

xanderphillips, 2024-08-18:
Page 21

CURRENTLY:
There are a few options when it comes to end stops. Hall Effect is a Voron stands as well as end stop switches. The team doesn’t provide the switch side, but we do have attachment points for and suppose to most common activation arms.

PROPOSED:
Hall Effect and mechanical switches both standard options for Voron end stops. The StealthChanger project does not cover the switch side but does have attachment points and support for most common activation arms.

TheSin-, 2024-08-20:
Thank you for this it is much appreciated, I will try to get this done as soon as I can.

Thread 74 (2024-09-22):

Trouble with QGL

sgermain06, 2024-09-22:
After printing everything I need for my Voron 2.4 350, following guides and all, ever since I installed the shuttle for stealthchanger and installed my dragonburner on it, I'm having some really weird issues with performing QGL. For some reason, the variations are all over the place. The toolhead seems to fit perfectly on the shuttle, it moves up and down freely, it doesn't feel loose or anything. Also, I have minimal variation when performing a PROBE_ACCURACY (usually under 0.003 variation) at all 4 corners. At first, I thought that maybe some of my Z steppers were out of order or something, but using the STEPPER_BUZZ command, I confirmed that they are all configured correctly.

Before I switched to this new setup, I had a single stealthburner with VoronTap and EBB2209 canbus board on Klipper v0.11 and had zero issues with QGL. I was also using all the same hardware, minus the Dragonburner and the EBB36.

Here's what I'm running:
Voron 2.4 350mm
Stealthchanger shuttle
Dragonburner toolhead (x2)
BTT Octopus Pro v1.1 (H723)
BTT EBB36 canbus breakout boards (x2)
BTT U2C

klipper - v0.12.0-302-g87ac693
klipper-toolchanger - v0.0.81-ge53f4233-inferred
moonraker - v0.9.0-g71f9e677
Raspberry Pi 4+ 8gb with Raspbian bullseye, fully updated

If anyone has any suggestion on how I could troubleshoot this, I'm all ears!

TheSin-, 2024-09-22:
98% of the time this is bad umbilicals or your mags are proud and you aren’t fully seated.  You should not see and pin or bushing at all when fully seated and you umbilicals should not push/pull on the tool at all you need a nice arc

if you are unsure please post pics but one of those will most likely fix everything

sgermain06, 2024-09-23:
I figured it out, well @techn0phreak figured it out lol! I had a Z-axis pulley that the set screw was loose (not sure how it happened, but it happened). I tightened everything back up, added some blue loctite and that thing is super solid now, QGL is going through without a problem.

Thanks for your suggestions!

Closed 2024-09-23.

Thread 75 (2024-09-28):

Install X Endstop Switch

pforrmi, 2024-09-28:
Hi!

Just for my understanding cause it's not that clear in the manual: How can I install a X Endstop Switch to that?
Hopefully someone could help.

Thanks!

And of course: Great job! Thanks for that.

TheSin-, 2024-09-28:
You do not install a switch to the shuttle which is why it’s not in the manual.  Please see the https://github.com/DraftShift/StealthChanger/tree/main/UserMods/VIN-y/Endstops if you want switches

Closed 2024-09-28.

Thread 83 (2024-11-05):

Heat insert clearance

gmihovics, 2024-11-05:
I was putting together my first shuttle and stealthburner backplates and I ran into some tolerance issues with heat inserts and my soldering iron. The first issue is the insert in the shuttle and its more just feedback. The insert went in with no problems but the plastic did bulge a little so I thought I share that.

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

The actual problem was with the stealthburner backplate. I have a stealth press zero with the generic soldering iron and the barrel of the soldering iron rubs the plastic of the backplate when putting in the top heat inserts. Here is a picture of the backplate after putting the insert in. I cleaned it up and I'm sure its going to work but again, I thought I would share my feedback if you weren't aware of the issue.

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

So far this has been a great build so thank you for all the effort.

Closed 2024-11-05.

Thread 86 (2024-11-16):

Faceplate

bronsn, 2024-11-16:
Hello, i try to use your Faceplate for XOL but the Plate dont fit to the Xol Toolhead.
It´s too big in height and the holes for the light are at the wrong place.

At the pic, right side is the original and left yours.

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

TheSin-, 2024-11-16:
We don’t release faceplates at all so not ours

Closed 2024-11-16.

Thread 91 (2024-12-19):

Add EBB SB2209 Comment to Configuration-CAN-Wiki

Neokil, 2024-12-19:
I just went through a lot of trial and error and with the help of the Draftshift discord I finally managed to get all my Toolheads to be recognized via CAN.
The Problem being that in contrast to all guides and most of the discord I had to add the resistor-jumper to every toolhead for it to work.
I think adding a small hint in the canbus-section (https://github.com/DraftShift/StealthChanger/blob/main/wiki/Configuration.md#canbus) like
```
Hint: If the tool-heads are not showing up on you can network try to add the 120 Ohm resistor to each of them. This solution is know to work on EBB SB2209 toolhead-boards.
```
could help a lot when you are setting canbus up for the project.

TheSin-, 2024-12-19:
this is not something we will add as we have seen this but it's random and seems to be U2C related.  This is something I have helped others with but it's not correct at all and I do not want to post miss information, this is something SB2209 should post if they seem fit to do so as it's their exception.

Closed 2024-12-19.

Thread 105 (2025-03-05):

Install is broken due to changes in tapchanger / klipper-toolchanger

kurtjcu, 2025-03-05:
Hi, Current changes to tapchanger and kjlipper-toolchanger mean that the installation guide will fail.

Also a user that updates tapchanger will no longer have the required files in the symlink.

## Work around(existing installation):
1. remove update info from moonraker.conf
2. checkout commit with correct files "git checkout a277492516af3751aa13f5097a908ab8a88b6eae" from within tapchanger dir.

## Work around(existing installation):
```
cd ~
git clone https://github.com/viesturz/tapchanger.git --no-checkout --depth 1 --filter=blob:none
cd tapchanger
git sparse-checkout init --cone
git sparse-checkout set Klipper
git checkout a277492516af3751aa13f5097a908ab8a88b6eae
cd ~
ln -s ~/tapchanger/Klipper/config-example ~/printer_data/config/tapchanger
```
Do NOT add to moonraker.conf as per instructions as this will update and cause the issue again.

TheSin-, 2025-03-05:
Thanks I'll add some info for this, until we release our version and make it main stream this will work.

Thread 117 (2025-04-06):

Anthead top mount hole "wrong way" around ?

ga73, 2025-04-06:
Hi, it seems the top hole on the carriage for anthead is the wrong way around.
Surely the indent for the screw head should be on the other side - i'm referring to the screw that holds the anthead main body - not the extruder.

Could this be corrected please :)

TheSin-, 2025-04-06:
Please join discord for help. It is not the wrong way as I have built over a dozen personally.  But on discord we can use pictures to help.  The screw is inserted before hand between the parts, the hole is so you can put an Allen wrench in to tighten it after assembly.

Closed 2025-04-06.

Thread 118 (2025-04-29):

WYC-H206 - "generic" optical sensor, will it work instead of the Optotap?

Marcos2BR, 2025-04-29:
It's low-cost, less than 1 USD each in Aliexpress.

The sensor works well with 5V, I've been using one of these for over 3 years on the "BFTPouch - Poor's man BLtouch" on my Hypercube.

**Do you guys with more experience think it could be used instead of the optotap?**

ps:
-I can't test it on my StealthChanger because I'm still assembling my Voron. Do you guys who know more about the project have anything to say?
-I think you only need to change a few things in the STL, just the fitting on the sensor.
I edited this STL to test fit (dragonburner V1.1 "**W**" ; _WYC-H206_ )
https://github.com/Marcos2BR/Voron-2/blob/Voron2.4/Addons/StealthChangerMods/Dragonburner_Legacy_wyc-h206.stl

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

TheSin-, 2025-06-14:
you'd have to try it, I don't find Opto taps that bad to buy, IIRC most can get them for like $5 on AliX.

But I can't see what it wouldn't work honestly.

Closed 2025-06-14.

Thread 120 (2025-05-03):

Document mentions unavailable assets.

aeiounix, 2025-05-03:
https://github.com/DraftShift/StealthChanger/tree/bef00555b1e31180e6e3ea8c880e65f3fc1085d8/UserMods/traxman25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

In the above link @traxman25 mentions DragonBurner_EBB36_OrbiterV2_mounts.STEP and a .3mf file which are not present in the repository.

TheSin-, 2025-05-03:
That’s a usermod, please contact the user on discord to report it

traxman25, 2025-05-05:
> https://github.com/DraftShift/StealthChanger/tree/bef00555b1e31180e6e3ea8c880e65f3fc1085d8/UserMods/traxman25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
>
> In the above link [@traxman25](https://github.com/traxman25) mentions DragonBurner_EBB36_OrbiterV2_mounts.STEP and a .3mf file which are not present in the repository.

The mount is in the 3mf located here: https://github.com/DraftShift/StealthChanger/blob/bef00555b1e31180e6e3ea8c880e65f3fc1085d8/UserMods/traxman25/Dragonburner_EBB36_SC_Mount/V1.0/DragonBurner_EBB36_Orb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

aeiounix, 2025-05-05:
Yeeaaah. I found it. Silly really. Thank you.

Closed 2025-05-03.

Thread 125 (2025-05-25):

Anthead backplate CAD is broken + missing older addons

aevesque, 2025-05-25:
Anthead sf backplate is broken and addons present in the earlier version are missing

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

nic335, 2025-05-25:
could you add more details?
what is broken and what addon is missing ?

seenit783, 2025-05-25:
This has been brought up before and I think its related to .stl. the cad is fine.

TheSin-, 2025-05-25:
Both where fixed long ago, as for the missing addons the mistake was including them before not the abcence of them

aevesque, 2025-05-26:
> This has been brought up before and I think its related to .stl. the cad is fine. Or it might be the opposite, I can't remember.

The above picture is a screenshot of the CAD from Fusion, yes the stl is fine

dt-justin, 2025-05-26:
maybe I fixed the A4T one now that I think about it.  I'll try to remember to re export it on the next run.

AstronIsTaken, 2025-06-09:
Can confirm, Anthead step file is broken. Fusion silently opens file but there are weird issues during modification, like all curves displayed as polygones. OnShape actually displays an error: "contains faulty topology" and doesn't show bottom face

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

Closed 2025-06-14.

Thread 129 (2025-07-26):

Interference between Stealthchanger Backplate and Shuttle

idonasch, 2025-07-26:
The Stealthchanger backplate  interferes with the shuttle in the recess between the top  dowels,  0.15mm more clearance is required on the rounded corners otherwise the shuttle does not slip on the toolhead without jamming.
I refer to the currently last STEP version of Stealthburner.STEP from  github version 8418f3d176a565976266675dca49a6b3b4ed128e from Jan 25.

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

SC0104

TheSin-, 2025-07-27:
Fixed in https://github.com/DraftShift/StealthChanger/commit/1c3050cfe53fa98924885a5075ad040a30844e1e

Thanks

Closed 2025-07-27.

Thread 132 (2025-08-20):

Sensorless homing x and y changes

pforrmi, 2025-08-20:
Just a stupid question cause I don' get it....

> Alternatively if you use sensorless for both you need so update G28 Y to use a copy of _SENSORLESS_HOME_X but for Y. There is a second place in the homing override that sets your Y rebound. The default is 20, without keeper you likely want this around 4-5, change G0 Y{ max_y - 20 } F5000 to G0 Y{ max_y - 5 } F5000 notice the 20 that changes. This is something you may need to adjust to figure out the position of your switch.

What I have to change to use sensorless homing for x and y?!

My current config section look like this:

```
[homing_override]
axes: xyz
gcode:
  INITIALIZE_TOOLCHANGER
  STOP_TOOL_PROBE_CRASH_DETECTION
  {% if printer.probe.last_query  %}
         RESPOND TYPE=echo MSG='Z Probe triggered, cannot home.'
  {% else %}
    SET_GCODE_OFFSET X=0.0 Y=0.0 Z=0.0
    {% set max_y = printer.configfile.config["stepper_y"]["position_max"]|float %}
    {% set home_all = 'X' not in params and 'Y' not in params and 'Z' not in params %}
    {% if home_all %}
      G90 ; absolute mode
      G28 Z
      G0 Z10 F1000
    {% endif %}
    {% if home_all or 'Y' in params or 'X' in params %}
      G28 Y
    {% endif %}
    {% if home_all or 'X' in params %}
      G90 ; absolute mode
      G0 Y{ max_y - 20 } F5000
      _SENSORLESS_HOME_X
      G91 ; relative mode
      G0 X-10 F5000
    {% endif %}
    {% if home_all or 'Z' in params %}
      {% set random_x = (range(-50, 50) | random) / 10 %}
      {% set random_y = (range(-50, 50) | random) / 10 %}
      G90 ; absolute mode
      G0 X{175.0+random_x} Y{175.0+random_y} F12000
      G28 Z
      _ADJUST_Z_HOME_FOR_TOOL_OFFSET
    {% endif %}
    _APPLY_ACTIVE_TOOL_GCODE_OFFSETS
    M400
  {% endif %}
```

nic335, 2025-08-21:
You would want to copy and modify macro _SENSSORLESS_HOME_X to Y and add it instead of doing the G28Y

Also, id recommend that you ask for help in our discord server, there is an awesome community there ready to help.
Make a ticket in help-and-support and we can help you thru-out the setup :)

https://discord.com/invite/draftshift

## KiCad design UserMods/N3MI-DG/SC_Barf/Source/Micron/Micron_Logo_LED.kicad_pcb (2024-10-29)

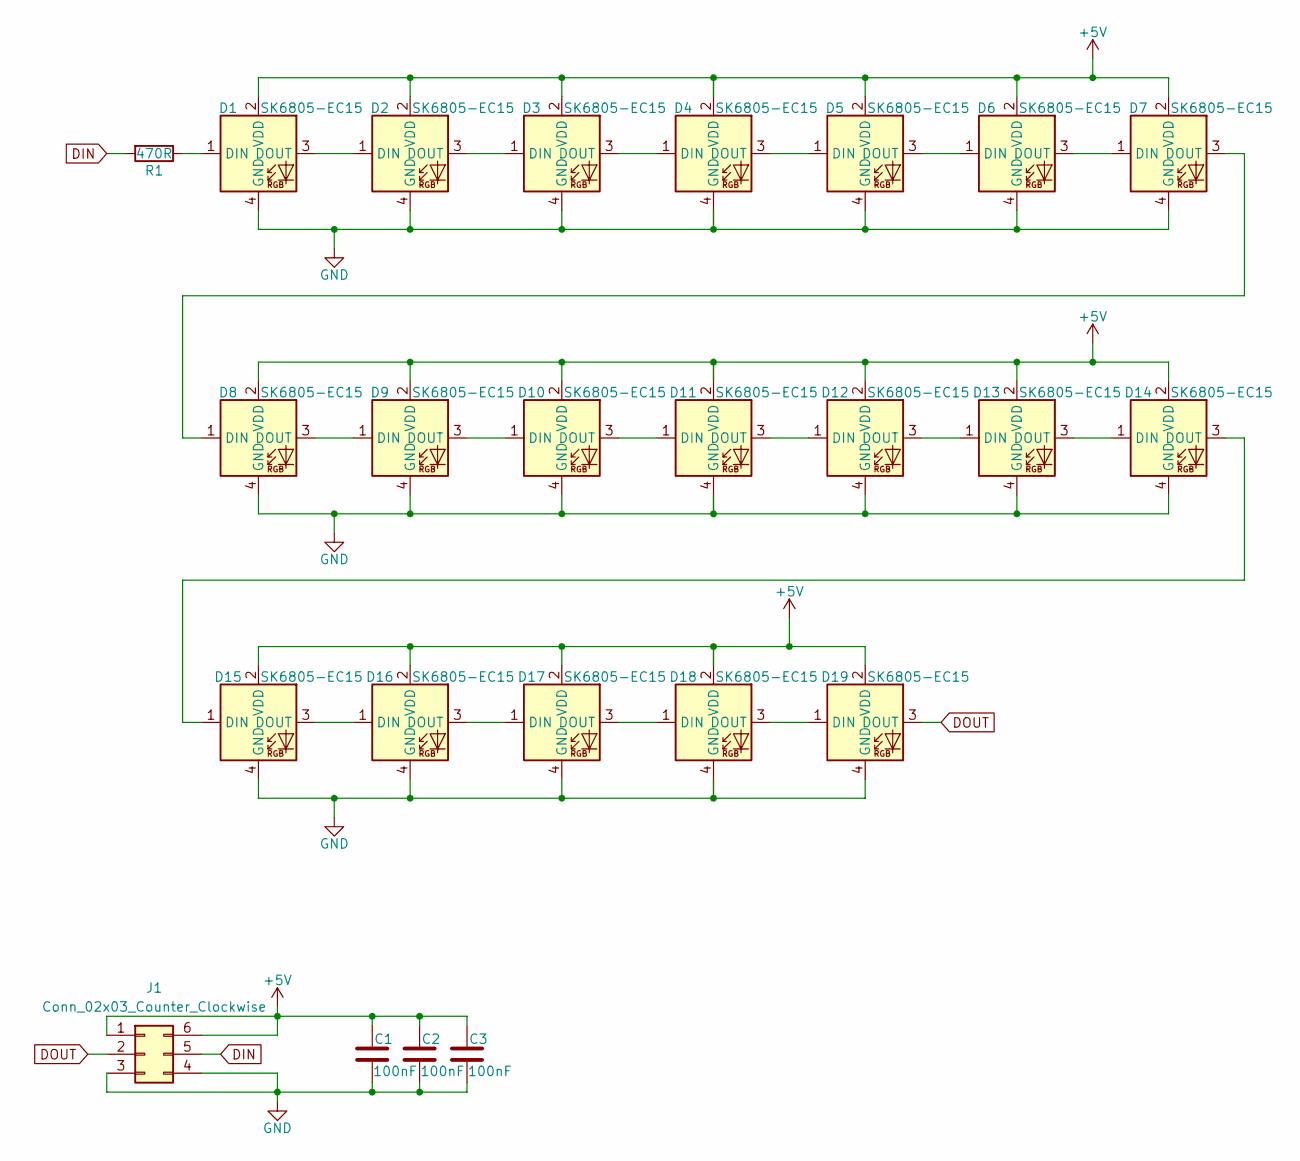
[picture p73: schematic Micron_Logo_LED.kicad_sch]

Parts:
C1, C2, C3: 100nF; C_0402_1005Metric; LCSC C14445
D1, D2, D3, D4, D5, D6, D7, D8, D9, D10, D11, D12, D13, D14, D15, D16, D17, D18, D19: SK6805-EC15; LCSC C2890035
J1: Conn_02x03_Counter_Clockwise; PinHeader_2x03_P2.54mm_Vertical_SMD
R1: 470R; R_0402_1005Metric; LCSC C25117

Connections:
+5V: C1.2, C2.2, C3.2, D1.2 (VDD), D2.2 (VDD), D3.2 (VDD), D4.2 (VDD), D5.2 (VDD), D6.2 (VDD), D7.2 (VDD), D8.2 (VDD), D9.2 (VDD), D10.2 (VDD), D11.2 (VDD), D12.2 (VDD), D13.2 (VDD), D14.2 (VDD), D15.2 (VDD), D16.2 (VDD), D17.2 (VDD), D18.2 (VDD), D19.2 (VDD), J1.1, J1.6
DIN: J1.5, R1.2
DOUT: D19.3 (DOUT), J1.2
GND: C1.1, C2.1, C3.1, D1.4 (GND), D2.4 (GND), D3.4 (GND), D4.4 (GND), D5.4 (GND), D6.4 (GND), D7.4 (GND), D8.4 (GND), D9.4 (GND), D10.4 (GND), D11.4 (GND), D12.4 (GND), D13.4 (GND), D14.4 (GND), D15.4 (GND), D16.4 (GND), D17.4 (GND), D18.4 (GND), D19.4 (GND), J1.3, J1.4
unnamed: D1.1 (DIN), R1.1
unnamed: D1.3 (DOUT), D2.1 (DIN)
unnamed: D2.3 (DOUT), D3.1 (DIN)
unnamed: D3.3 (DOUT), D4.1 (DIN)
unnamed: D4.3 (DOUT), D5.1 (DIN)
unnamed: D5.3 (DOUT), D6.1 (DIN)
unnamed: D6.3 (DOUT), D7.1 (DIN)
unnamed: D7.3 (DOUT), D8.1 (DIN)
unnamed: D8.3 (DOUT), D9.1 (DIN)
unnamed: D9.3 (DOUT), D10.1 (DIN)
unnamed: D10.3 (DOUT), D11.1 (DIN)
unnamed: D11.3 (DOUT), D12.1 (DIN)
unnamed: D12.3 (DOUT), D13.1 (DIN)
unnamed: D13.3 (DOUT), D14.1 (DIN)
unnamed: D14.3 (DOUT), D15.1 (DIN)
unnamed: D15.3 (DOUT), D16.1 (DIN)
unnamed: D16.3 (DOUT), D17.1 (DIN)
unnamed: D17.3 (DOUT), D18.1 (DIN)
unnamed: D18.3 (DOUT), D19.1 (DIN)

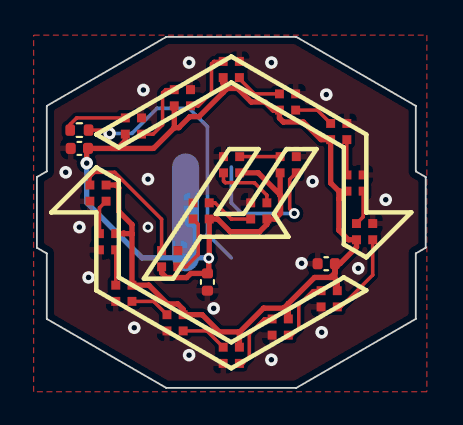
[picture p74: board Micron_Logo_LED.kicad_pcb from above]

Board: 2 copper layers, 21.6 x 19.5 mm, 24 parts (1 on the bottom side), 23 nets.

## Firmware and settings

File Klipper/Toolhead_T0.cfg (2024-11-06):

# If you are using CAN, define the board info
[mcu EBBT0]
canbus_uuid: xxxxxxxxxxx

# Extruder Example, change as needed. If this is T1, then should be something like extruder1
[extruder]
step_pin: EBBT0:PD0
dir_pin: !EBBT0:PD1
enable_pin: !EBBT0:PD2
microsteps: 16
full_steps_per_rotation: 200 # Single-turn pulse number (200 is 1.8 degrees, 400 is 0.9 degrees)
rotation_distance: 22.67895 # Driving pulley circumference mm
## Calibration step value: rotation_distance = <old rotation_distance> * <actual extrusion length> / <requested extrusion length>
gear_ratio: 50:10 # Reduction ratio (Galileo gear ratio 7.5:1 and comment out this line; BMG is 50:17, output shaft in front, input shaft in rear)
nozzle_diameter: 0.400 # Nozzle diameter
filament_diameter: 1.750 # filament diameter
heater_pin: EBBT0: PB13 # Extrusion head heating rod control pin setting (e0)
sensor_type: MAX31865 #Generic 3950 #MAX31865 # Sensor model
spi_bus: spi1
rtd_nominal_r: 100
rtd_reference_r: 430
rtd_num_of_wires: 2
sensor_pin: EBBT0: PA4 # Extrusion head sensor Pin (T_E0)
max_power: 1.0 # Heating rod PWM maximum output power
min_temp: -235 # Minimum temperature of extruder
max_temp: 500 # Maximum temperature of extruder
min_extrude_temp: 150 # The minimum extrusion temperature of the heating rod (the extruder can only perform extrusion when it reaches this temperature)
pressure_advance: 0.04 # Extruder pressure advance parameter
pressure_advance_smooth_time:0.040 # Smooth advancement time - the default value is 0.040
#Nozzle temperature PID calibration command: "PID_CALIBRATE HEATER=extruder TARGET=245
control=pid
pid_kp = 26.213
pid_ki = 1.304
pid_kd = 131.721
max_extrude_only_distance: 1400.0
max_extrude_only_velocity: 75.0
max_extrude_only_accel: 1500


[tmc2209 extruder]
uart_pin: EBBT0: PA15
interpolate: False
run_current: 0.6
sense_resistor: 0.110
stealthchop_threshold: 0 # Silence threshold (if silence is not required, please change the value to 0)

# Change tool number if needed here
[multi_fan T0_partfan]
pin: EBBT0:PA1

# Change tool number if needed here
[heater_fan T0_hotend_fan]
pin: EBBT0:PA0
# Change extruder tool number if needed here
heater: extruder
heater_temp: 50.0
kick_start_time: 0.5

#Change tool number if needed in the next line, as well ast the last line
[gcode_macro T0]
variable_color: ""
gcode:
  SELECT_TOOL T=0

#change the tool numbers to the tool you are configuring, ie T0, T1, etc
[tool T0]
#change this too
tool_number: 0
#if this were T1, then this would be extruder1, etc
extruder: extruder
#Change T0_partfan to tool number
fan: multi_fan T0_partfan
gcode_x_offset: 0
gcode_y_offset: 0
gcode_z_offset: 0
params_type: 'sc'
#This is the path the tool change takes. Shouldn't have to change it. Unless
#you are using a custom dock
params_sc_path: [{'y':9.5 ,'z':4}, {'y':9.5, 'z':2}, {'y':5.5, 'z':0}, {'z':0, 'y':0, 'f':0.5}, {'z':-10, 'y':0}, {'z':-10, 'y':16}]
#These are build specific, its where the tool is sititng in it's dock.
params_park_x: 28
params_park_y: -71.0
params_park_z: 381.0
params_safe_y: 20.0
# For InputShaper run per tool and enter the frequency here
params_input_shaper_type_x: 'mzv'
params_input_shaper_freq_x: 62.4
params_input_shaper_damping_ratio_x: 0.01
params_input_shaper_type_y: 'mzv'
params_input_shaper_freq_y: 88.6
params_input_shaper_damping_ratio_y: 0.01

# Change tool number if needed
[tool_probe T0]
pin: ^EBBT0:PB6
tool: 0
x_offset: 0 # X axis-sensor relative nozzle offset
y_offset: 0 # Y axis-sensor relative nozzle offset
z_offset: 0 # Z axis-sensor relative nozzle offset
# drop_first_result: True # enable is on danger-klipper
speed: 5.0
samples: 3
samples_result: median
sample_retract_dist: 2.0
samples_tolerance: 0.02
samples_tolerance_retries: 3
activate_gcode:
    _TAP_PROBE_ACTIVATE HEATER=extruder

[adxl345 T0]
cs_pin: EBBT0:PB12
spi_software_sclk_pin: EBBT0:PB10
spi_software_mosi_pin: EBBT0:PB11
spi_software_miso_pin: EBBT0:PB2
axes_map: x,z,y

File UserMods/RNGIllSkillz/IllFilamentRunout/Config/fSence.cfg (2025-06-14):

[mcu fSense]
canbus_uuid: "your_uuid"

[temperature_sensor fSense_temp]
sensor_type: temperature_mcu
sensor_mcu: fSense
min_temp: 1
max_temp: 75

[gcode_macro SET_EXTRUDER_SENSOR]
description: Enable or disable filament sensor(s) for specific extruder(s).
  Parameters:
    TOOL: Extruder number (e.g., 0, 1, etc.) or -1 for all configured tools (default 0).
    ENABLE: Sensor state (0=disable, 1=enable, default 1).
  Examples:
    SET_EXTRUDER_SENSOR TOOL=0 ENABLE=1   ; Enable RunOutExtruder0
    SET_EXTRUDER_SENSOR TOOL=2 ENABLE=0   ; Disable RunOutExtruder2
    SET_EXTRUDER_SENSOR TOOL=-1 ENABLE=0  ; Disable all configured sensors
gcode:
    {% set tool = params.TOOL|default(0)|int %}
    {% set enable = params.ENABLE|default(1)|int %}

    # Validate ENABLE
    {% if enable not in [0, 1] %}
        { action_raise_error("Invalid ENABLE value. Must be 0 or 1.") }
    {% endif %}

    # Check if toolchanger is configured
    {% if printer.toolchanger is not defined %}
        { action_raise_error("Toolchanger not configured. Cannot retrieve tool numbers.") }
    {% endif %}

    # Get configured tool numbers
    {% set tools = printer.toolchanger.tool_numbers %}
    {% if tools|length == 0 %}
        { action_raise_error("No tools configured in toolchanger.") }
    {% endif %}

    # Handle all tools (TOOL=-1)
    {% if tool == -1 %}
        {% for t in tools %}
            {% set fiSense = "RunOutExtruder" ~ t %}
            {% if printer["filament_motion_sensor " ~ fiSense] is defined %}
                SET_FILAMENT_SENSOR SENSOR={fiSense} ENABLE={enable}
                RESPOND TYPE=echo MSG="Filament sensor {fiSense} {'enabled' if enable else 'disabled'}"
            {% else %}
                RESPOND TYPE=error MSG="Filament sensor {fiSense} not found"
            {% endif %}
        {% endfor %}
    {% else %}
        # Validate TOOL
        {% if tool not in tools %}
            { action_raise_error("Invalid TOOL value. Must be one of: " ~ tools|join(", ")) }
        {% endif %}

        # Toggle single sensor
        {% set fiSense = "RunOutExtruder" ~ tool %}
        {% if printer["filament_motion_sensor " ~ fiSense] is defined %}
            SET_FILAMENT_SENSOR SENSOR={fiSense} ENABLE={enable}
            RESPOND TYPE=echo MSG="Filament sensor {fiSense} {'enabled' if enable else 'disabled'}"
        {% else %}
            { action_raise_error("Filament sensor {fiSense} not found") }
        {% endif %}
    {% endif %}

[filament_motion_sensor RunOutExtruder0]
detection_length: 10   
extruder: extruder
switch_pin: fSense:gpio21 
pause_on_runout: false
runout_gcode: 
    bRunOut 
    RESPOND TYPE=error MSG="Filament runout detected on Extruder0"              
    PAUSE

[filament_motion_sensor RunOutExtruder1]
detection_length: 10   
extruder: extruder1
switch_pin: fSense:gpio20 
pause_on_runout: false
runout_gcode: 
    bRunOut
    RESPOND TYPE=error MSG="Filament runout detected on Extruder1"               
    PAUSE

[filament_motion_sensor RunOutExtruder2]
detection_length: 10   
extruder: extruder2
switch_pin: fSense:gpio19 
pause_on_runout: false
runout_gcode: 
    bRunOut   
    RESPOND TYPE=error MSG="Filament runout detected on Extruder2"            
    PAUSE

[filament_motion_sensor RunOutExtruder3]
detection_length: 10   
extruder: extruder3
switch_pin: fSense:gpio18 
pause_on_runout: false
runout_gcode: 
    bRunOut  
    RESPOND TYPE=error MSG="Filament runout detected on Extruder3"             
    PAUSE

[filament_motion_sensor RunOutExtruder4]
detection_length: 10   
extruder: extruder4
switch_pin: fSense:gpio17 
pause_on_runout: false
runout_gcode: 
    bRunOut
    RESPOND TYPE=error MSG="Filament runout detected on Extruder4"               
    PAUSE

[filament_motion_sensor RunOutExtruder5]
detection_length: 10  
extruder: extruder5
switch_pin: fSense:gpio16 
pause_on_runout: false
runout_gcode: 
    bRunOut               
    RESPOND TYPE=error MSG="Filament runout detected on Extruder5"
    PAUSE

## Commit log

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2023-12-02 made mount more robust to avoid snapping
    [Shuttle.3mf, mount.3mf]
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2023-12-12 Add v24 with 45 steps on the bottom to help rigidity at full lock position
    [StealthChanger_Tripod_v24.step, StealthChanger_Tripod_v24_Back_Plate.stl, StealthChanger_Tripod_v24_Hall_Effect.stl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]
2023-12-12 Back Plate - add the chamfer back in at the CW2 mount point (made it weaker there) - leveled the flat surface on the front of the dual magnets - cleaned up a few stray chamfers in the center hole - m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
    Hall Effect
    - thickened up the plastic around the mount hole (kept spliting)
    - cut out 0.1 of the mount hole
    Shuttle
    - added 0.05 on the magnet holes on the 45 slope
    - remove 0.2 from teh rail mount insets (inset the screws more, hitting magnets)
    [StealthChanger_Tripod_v25.step, StealthChanger_Tripod_v25_Back_Plate.stl, StealthChanger_Tripod_v25_Hall_Effect.stl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]
2023-12-12 Back Plate - Fix heatset insert holes 4.6 -> 4.7 - Fix CS screw head size 6.0 -> 6.1
    [StealthChanger_Tripod_v26.step, StealthChanger_Tripod_v26_Back_Plate.stl, StealthChanger_Tripod_v26_Hall_Effect.stl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]
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2023-12-13 Back Plate - Add chamfer on the top inner corner where the tap tower is, was a weak point - Rebuilt the entire tap tower, the holes were a little far back
    [StealthChanger_Tripod_v27.step, StealthChanger_Tripod_v27_Back_Plate.stl, StealthChanger_Tripod_v27_Hall_Effect.stl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]
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2023-12-13 Replace 3mf files with pre-oriented stl files
    [StealthChanger_Tripod_v28_Back_Plate.3mf, StealthChanger_Tripod_v28_Back_Plate.stl, StealthChanger_Tripod_v28_Hall_Effect.3mf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]
2023-12-15 rebranded tripod version as rev3 to avoid nesting
    [StealthChanger_Tripod_v24.step, StealthChanger_Tripod_v24_Back_Plate.stl, StealthChanger_Tripod_v24_Hall_Effect.stl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]
2023-12-15 Back Plate - Changed the tap sensor tower no longer have round ends for cleaner printing - Made sure the tap sensor tower was completely centered
    - Removed heatset insert hole for the old Hall Effect bracket
    Misc
    - Removed old Hall Effects bracket, this is so all brackets can use one mount point
    - Added shuttle keeper for 6mm belts
    - Added shuttle keeper for 9mm belts
    - Added X Endstop bracket from TapChanger (Slightly modded to fit)
    - Added Hall Effect bracket from TapChanger (Slightly modded to fit)
    - Added Hall Effect bracket modded to work with the shuttle keeper which changed the alignment
    NOTES
    - Kept the 8mm bushing version but I feel this could be merged now
    - Added the f3d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
    [Shuttle_Keeper_6mm.stl, Shuttle_Keeper_9mm.stl, StealthChanger_Tripod_v29.f3d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]
2023-12-16 Shuttle - Cut some of the top off to make more room for the v30 Back Plate changes - Removed 0.5mm between the top magnets by moving it down a little, we want the pins to fully engage and not have th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
    Endstops
    - Changed the thickness of the attach point of the Hall Effects bracket
    - Removed material from the shuttle keeper version of the Hall Effects
    f3d
    - disolved all actions to clean up the file
    NOTE:
    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
    [StealthChanger_Tripod_v31.f3d, StealthChanger_Tripod_v31.step, StealthChanger_Tripod_v31_Back_Plate_SB.stl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]
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2023-12-18 Shuttle - The belt loop gap on each side wasn't the same, corrected it
    Back Plate (SB)
    - Top magent was 6.1, changed to 6.2 round to match the shuttle
    - Added a seat to the magnets on 45
    Hall Effects (both)
    - Open the magnet holes form 5.8 to 6.1 hex
    - Deeped the magnet hole so it site flush and straight
    - Added a seat to the magnet
    [StealthChanger_Tripod_v32.f3d, StealthChanger_Tripod_v32.step, StealthChanger_Tripod_v32_Back_Plate_SB.stl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]
2023-12-20 Endstop - Fix an odd face on the Hall Effect version
    - Remove a large section of the mid, it was extra printing and this allows for a much longer dock/undock motion
    - Make the carriage holes 4mm instead of 3.8mm for better bolt sizes
    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
    [StealthChanger_Tripod_v33.f3d, StealthChanger_Tripod_v33.step, StealthChanger_Tripod_v33_Back_Plate_SB.stl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]
2023-12-21 Shuttle - Added Fillet to the Bottom of the top bar - Added belt grooves for those that don't want to loose 5mm to the shuttle keeper, belt groves are for 6 and 9 mm belts - Adjusted the bolts for th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
    [StealthChanger_Tripod_v34_Back_Plate_SB.stl, StealthChanger_Tripod_v34_Endstop_Hall_Effect.stl, StealthChanger_Tripod_v34_Endstop_Hall_Effect_Shuttle_Keeper.st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]
2023-12-21 e organize the repo, as we near a release version lets remove the versions and start working on a singular version
    [Mount hall effect.3mf, Mount.3mf, Shuttle.3mf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]
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2023-12-22 Move to shorter names and directories
    [Endstop_Hall_Effect_Shuttle_Keeper.stl, Endstop_Switch_fiferboy.stl, Hall_Effect.stl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]
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2023-12-23 Sorry this is the optitap version, moving back to main, unclicky version is still a WIP
    [Dragonburner.stl, Dragonburner_Spacer.stl]
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2023-12-25 CAD - Change to components
    Back Plates
    - Add logo to each plate
    - Dragonburner add 45 so that it can be printed without supports
    [Dragonburner.stl, StealthChanger.f3d, Stealthburner.stl]
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2023-12-26 Path is sound, just need to figure out why it's checking for a dock before the sensoris triggered
    [printer-T0.cfg]
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2023-12-28 README - updated for Dargonburner BOM and Notes
    Back Plate
    - Dragonburner convert nuts to heat inserts as per voron standards
    - Dragonburner add optional pan head m3 to the spacer
    [Dragonburner.stl, Dragonburner_Spacer.stl, StealthChanger.f3d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]
2023-12-30 Add UserMod for Beefing up Shuttle and Back Plate
    I am not yet confident these changes are worthy of the mainline so
    I've added them as a UserMod.
    [Back_Plates-Stealthburner-Beefy.stl, Shuttle-ThroughHole.stl, Shuttle_Keeper-ThroughHole.stl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]
2024-01-06 Shuttle - Lots of changes to try to remove all flex - Optional m3x40 SHCS screws for added stiffness
    - All endstops modified to fit the new shuttle
    - Dragon burner was redesigned. New matches the body and flow of the DB
    - Added wire channels for easier wiring
    - Spacer redesigned to flow and easier to install
    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
    [Dragonburner.stl, Dragonburner_Spacer.stl, Endstop_Hall_Effect_Shuttle_Keeper.stl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]
2024-01-06 Add notes about the optional stiffening screws
2024-01-06 Fix typo
    [printer-T0.cfg]
2024-01-08 Back Plate - Update the Dragon Burner spacer to allow wiring to pass
    step file was too large, start compressing it
    [Dragonburner_Spacer.stl]
2024-01-08 Convert giant step file to smaller files that no longer contain the hotends
    [StealthChanger_Dragonburner.step, StealthChanger_Shuttle.step, StealthChanger_Stealthburner.step]
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2024-01-09 XY Endstops Assembly (#2)
    * Add files via upload
    * Create README.MD
    * Delete UserMods/VIN-y/README.MD
    * Create README.md
    * Delete UserMods/X-trigger_v1-Body001.step
    * Delete UserMods/Endstops-Carrier_v3-Body001.step
    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
    [Endstops-Carrier_v3-Body001.stl, X-trigger_v1-Body001.step, X-trigger_v1-Body001.stl]
2024-01-10 Add Ball Trigger for tool calibration
    - standard Voron microswitch and 12 mm ball bearing required
    [Ball_Trigger_V4-Body.stl, Ball_Trigger_V4-Cap.stl, Ball_Trigger_V4.step]
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2024-01-17 Add version of StealthChanger for Stealburner with D2HW
    - D2HW-C203MR switches required for this version
    - Shuttle is modified to remove the upper lip and pin
    - D2HW triggers against the MGN12 carriage (with Shuttle-Keeper)
    - This is the "beefy" version from the fiferboy UserMod
    [Shuttle_Beefy_D2HW.stl, StealthChanger_D2HW.step, Stealthburner_Beefy_D2HW.stl]
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2024-01-20 Add files via upload
    Added new version with beefed tension mounts and added 6mm branding
    [Left Block.stl, Left Clip.stl, Right Block.stl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]
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2024-01-24 Adding a leg to the shuttle
    Allows the shuttle to use a standard Z Endstop without a tool attached
    [DB Z Foot.step, DB Z Foot.stl, SB Z Foot.step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]
2024-01-31 add StealthChanger Xol-Toolhead (#11)
    * add Xol-Toolhead UserMod
    add Xol-Toolhead UserMod with dock
    * Update README_Xol-Toolhead.md
    [StealthChanger_Xol-Toolhead_EBB36_Mount.step, StealthChanger_Xol-Toolhead_EBB36_Mount.stl, StealthChanger_Xol-Toolhead_Plate.step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]
2024-01-31 Rename dir since it's redundant and long, rename readme so it shows on github properly
    [StealthChanger_Xol-Toolhead_EBB36_Mount.step, StealthChanger_Xol-Toolhead_EBB36_Mount.stl, StealthChanger_Xol-Toolhead_Plate.step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]
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2024-02-05 Beefy shuttle for 9mm belts
    Included a beefy shuttle with a split keeper to allow east tensioning of 9mm belts. especially required for AWD
    [Keeper for 9mm x2.stl, Shuttle for 9mm.stl]
2024-02-06 Shouldn't be in main, no docu, no CAD, no info, and confuses users
    [Shuttle_Beefy_D2HW.stl]
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2024-02-27 Fix brackets in right Markdown order
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2024-03-01 Add DB Cowl and EBB36-OrbiterV2 mount (#24)
    * Update README.md
    Update instruction for what the mod is and how to use it.
    * Delete UserMods/traxman25/Dragon Burner Mods directory
    * Add DB_Cowl directory
    * Upload DB numbered cowls
    Added Dragonburner numbered cowls, diffusers and led carriers.
    * Delete UserMods/traxman25/Dragonburner_Numbered_Cowls/temp
    * Create Dragonburner_EBB36_SC_Mount
    * Delete UserMods/traxman25/Dragonburner_EBB36_SC_Mount
    * Create temp
    * Add Dragonburner EBB26 OrbiterV2 mount set
    * Delete UserMods/traxman25/Dragonburner_EBB36_SC_Mount/temp
    * Create temp
    * Add photos to show mods
    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
    [0 diffuser.STEP, 1 diffuser.STEP, 2 diffuser.STEP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]
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2024-03-03 Add mention of the shuttle to carriage screw type, and fix a typo
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2024-03-14 6mm Shuttle Keeper fix
    [Shuttle_Keeper_6mm.stl]
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2024-04-01 Update Toolhead_T1.cfg (#41)
    Fixed extruder1 hotend fan
    [Toolhead_T1.cfg]
2024-04-01 Add Filament Sensor version. Update screw guidance. Add images. Fix typos. (#40)
    * Add optional filament sensor version, change guidance on screws, add photos, update docs
    * Update Readme for filament sensor version and screw guidance
    * Fix typos
    * fix typos
    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
    [DB_EBB36_Orbiter2.0_wFSensor_Mount.1.0.f3d, DB_EBB36_Orbiter2.0_wFSensor_Mount.1.0.step]
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2024-04-11 Flisher's PTFE Breakout Block and Temporary Backplate (#45)
    * Adding Flisher Backplate and PTFE Breakout Block
    * Renamed Backplate to Temporary_Backplate, added a picture
    * fixing image
    * Moving image at the end
    * fixing link
    [Flisher-PTFE_Breakout_Block_Main-v3.1.stl, Flisher-PTFE_Breakout_Block_Secondary-v3.1.stl, Flisher-Temporary_Backplate-V2.STEP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]
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2024-05-07 Xol support added for Short and Medium ducts
    [StealthChanger_Xol.step, Xol_Medium.stl, Xol_Short.stl]
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2024-06-17 Add files via upload
    Fixed MGN9H shuttler keeper for correct vertical belt spacing for Micron and other printers for ants.
    [SC V1.1 Shuttle And Keeper Micron.step, ShuttleKeeperMicron.stl]
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2024-06-17 Rename Shuttle MGN12 (WIth belt grooves).stl to Shuttle MGN12 (With belt grooves).stl
    Fix filename typo
    [Shuttle MGN12 (With belt grooves).stl]
2024-06-17 Rename Shuttle MGN12 (WIthout belt grooves).stl to Shuttle MGN12 (Without belt grooves).stl
    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
    [Shuttle MGN12 (WIthout belt grooves).stl, Shuttle MGN12 (Without belt grooves).stl]
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2024-06-25 Very minor clearance and printability fixes
    [BlackBird Medium.stl, BlackBird Short.stl, BlackBird.step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]
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2024-06-30 Add Z_Belt_Covers, Rename to remove spaces in files/dirs, add missing readme files with designer credits
    [Belt_Cover_A.stl, Belt_Cover_B.stl, BlackBird_Medium.stl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]
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2024-06-30 Fix logo on A side
    [V2_Belt_Covers_SC.step]
2024-06-30 Fix step file
    [V2_Belt_Covers_SC.step]
2024-07-02 Try to fix the files again
    [Belt_Cover_A.stl, Belt_Cover_B.stl, Logo_A.stl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]
2024-07-03 Fix merging B side
    [Belt_Cover_A.stl, Belt_Cover_B.stl, Logo_B.stl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]
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2024-07-11 Rounding error in CAD fixed
    [BlackBird Medium.stl, BlackBird Short.stl, BlackBird.step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]
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2024-07-25 ECAS file fix (#60)
    [ecas_entry_2.5mm.step, ecas_entry_2.5mm.stl, ecas_entry_3mm.step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]
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2024-08-27 Xol fix + Yavoth UHF backplate added
    [XOL.step, XOL_Medium.stl, XOL_Short.stl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]
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2024-09-12 Yavoth UHF fix
    [Yavoth UHF.step, Yavoth UHF.stl]
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2024-09-14 OB2 wasn't ready yet, something is wrong with my CAD as it doesn't even come close IRL
    [OB2_PCBMount.step, OB2_PCBMount.stl]
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2024-09-14 Fix thin walls
    [OB2_Spacer.step, OB2_Spacer.stl]
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2024-10-03 Fix file names
    [LED_holder.stl, Orbitor-Dragon.stl, Orbitor-Revo.stl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]
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2024-10-05 Add more clearance to EBB36 cover (#79)
    [EBB36_Cover.stl]
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2024-10-13 Update to fix the fact that the docks wouldn't clear properly at the top
    [Bracket_Left.stl, Bracket_Right.stl, SV08_Dockbar_Brackets.step]
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2024-10-21 Update link as 30mm was missing
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2024-11-27 Add missing version stamp
    [A4T.step, A4T.stl, XOL.step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]
2024-11-28 Add 0.05 more tolerance in the logo area
    [Cover_A.stl, Cover_B.stl, V2_Belt_Covers_SC_v12.step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]
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2024-12-14 Add missing gantry extrusions
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2025-01-06 Anthead nozzle led fix (#98)
    * ANTHEAD NOZZLE LED FIX
    A simple modification of N3MI's original LED for the SF ANTHEAD. Main bodies are labeled VORON LOGO. LED's are labeled LED. You must split the LED to objects in slicer and orient correctly.
    * Create ANTHEAD_NOZZLE_LED_FIXES.md
    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
    [HF_ANTHEAD_NOZZLE_LED.step, HF_ANTHEAD_ORBITER_VORONLOGO.step, HF_ANTHEAD_SHERPAMINI_VORONLOGO.step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]
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2025-01-18 Update for a slight interference with the new NH36
    [PCBMount.step, PCBMount.stl]
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2025-02-03 Fix missing holes on the Yavoth_UHF
    [Yavoth_UHF.stl]
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2025-03-02 Fix Anthead backplate, was out by 1mm
    [Anthead.step, Anthead_HF.stl, Anthead_SF.stl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]
2025-03-03 Fix missing face in the step file
    [Anthead.step]
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2025-03-07 wiki-FAQ entry for short tools and z-rail-limits and update old xol readme (#107)
    * delete old folder due to rename and merge
    * add wiki entry for issue with short tools and z-rail-travel limit
    add wiki entry for issue with short tools and z-rail-travel limit
    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
2025-03-14 Fix Klipper README links (#108)
    Fix the links to the TapChanger files in the Klipper README.
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2025-03-28 Correction, Micron uses 19 LEDs
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2025-06-14 Fix an issue with Anthead exports
    [Anthead.step, Anthead_HF.stl, Anthead_SF.stl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]
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2025-07-27 Fix a very small interference
    [StealthBurner.step, StealthBurner.stl]
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2025-10-28 Update of my prior mod to rectify problem found and added PCB mount for Anthead SF with WWG2 (#137)
    * Update Repo Location for per tool probe to current location
    * Added Anthead SF WWG2 Setup and Rev 9 for Sherpa Mini
    * Added additional readme
    * Revise readme for Anthead Sherpa Mini EBB 36 PCB Mount
    Updated readme to reflect improvements in revision 9, including enhanced spring steel captur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
    [Anthead Back Plate SF WWG2.stl, PCB Mount Anthead SF WWG2.stl, PCBMount V9.stl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]
2025-10-28 UsrMod Add CHCB-V HotEnd Mount For Anthead (#135)
    * UsrMod_CHCB-V Mount initial comit
    * UsrMod CHCB-V Fix
    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
    [CHCB-V V6DM-SF.step, CHCB-V V6DM-SF.stl]
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2025-10-30 Add low-profile PG7 mount for printed A motor to provide USB/CAN clearance in rear corner
    [printed_gantry_pg7_mount.step]
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2025-11-03 Fix orientantation
    [DragonBurner with Trax-ears R1.stl, DragonBurner.stl]
2025-11-03 Add low-profile pg7 mount companion modification to CNC shuttle mounts for Beacon/Carto (#138)
    * Add low-profile pg7 gantry mounts, images and update readmes
    * Fix image paths in Readme
    * Fix more image paths in readmes
    * Add additional verbiage explaining what this does
    [chaotic_cf_pg7_mount.step, chaotic_cnc_pg7_mount.step, chaotic_motor_mount_insert.step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]
2025-11-06 Fix the ear placement as per Issue #140
    [DragonBurner with Trax-ears R1.stl]
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2025-11-12 Add v1.1 and update v1.0 with ldo/fystec specific top plates (#142)
    * Fix broken link to PG7 in Readme
    * Fix broken link to PG7 in Readme
    * Fix broken link to PG7 in Readme
    * Fix broken link to PG7 in Readme
    * Add Fystec/LDO specific flag plates to account for screw spacing
    * add v1.1 .step, images and Readme
    * Add link to 1.1 in Readme
    * Add png files and fix typos in Readme
    * Add example .cfg file and install script for tool_crash
    * Update Readme to new install instructions and .cfg example
    * Fix typo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
    [fystec_inserts.step, fystec_top_flag_plate_2020.step, fystec_top_flag_plate_2020_backer.step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]
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2025-12-03 Add v1.2 and correct some v1.1 components (#146)
    * Update README.md path to install to raw
    install path needs to be raw to ensure it will execute
    * Add v1.2, update readmes and correct v1.1 submissions
    * Formatting changes
    * add testing short mount with pcb moved to rear
    [fystec_inserts.step, fystec_top_flag_plate_2020.step, fystec_top_flag_plate_2020_backer.step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]
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2025-12-03 Add missing DB backplate
    [DragonBurner.stl]
